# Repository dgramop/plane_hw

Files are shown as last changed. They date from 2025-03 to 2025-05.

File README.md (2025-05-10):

# Plane Hardware

Board Design Rev1 Mistakes:
- Wrong footprint for the PX4 connector on the pitot. Accidentally used the same one as all the I2C busses. Already have these connectors
- Forgot to order MALE connectors that go on the board. JST female is the for the cable. Whoops

Rev 2 Wishlist:
- Better harnessing - fewer things to connect + better modularity. Then we can have test beds for each part in isolation

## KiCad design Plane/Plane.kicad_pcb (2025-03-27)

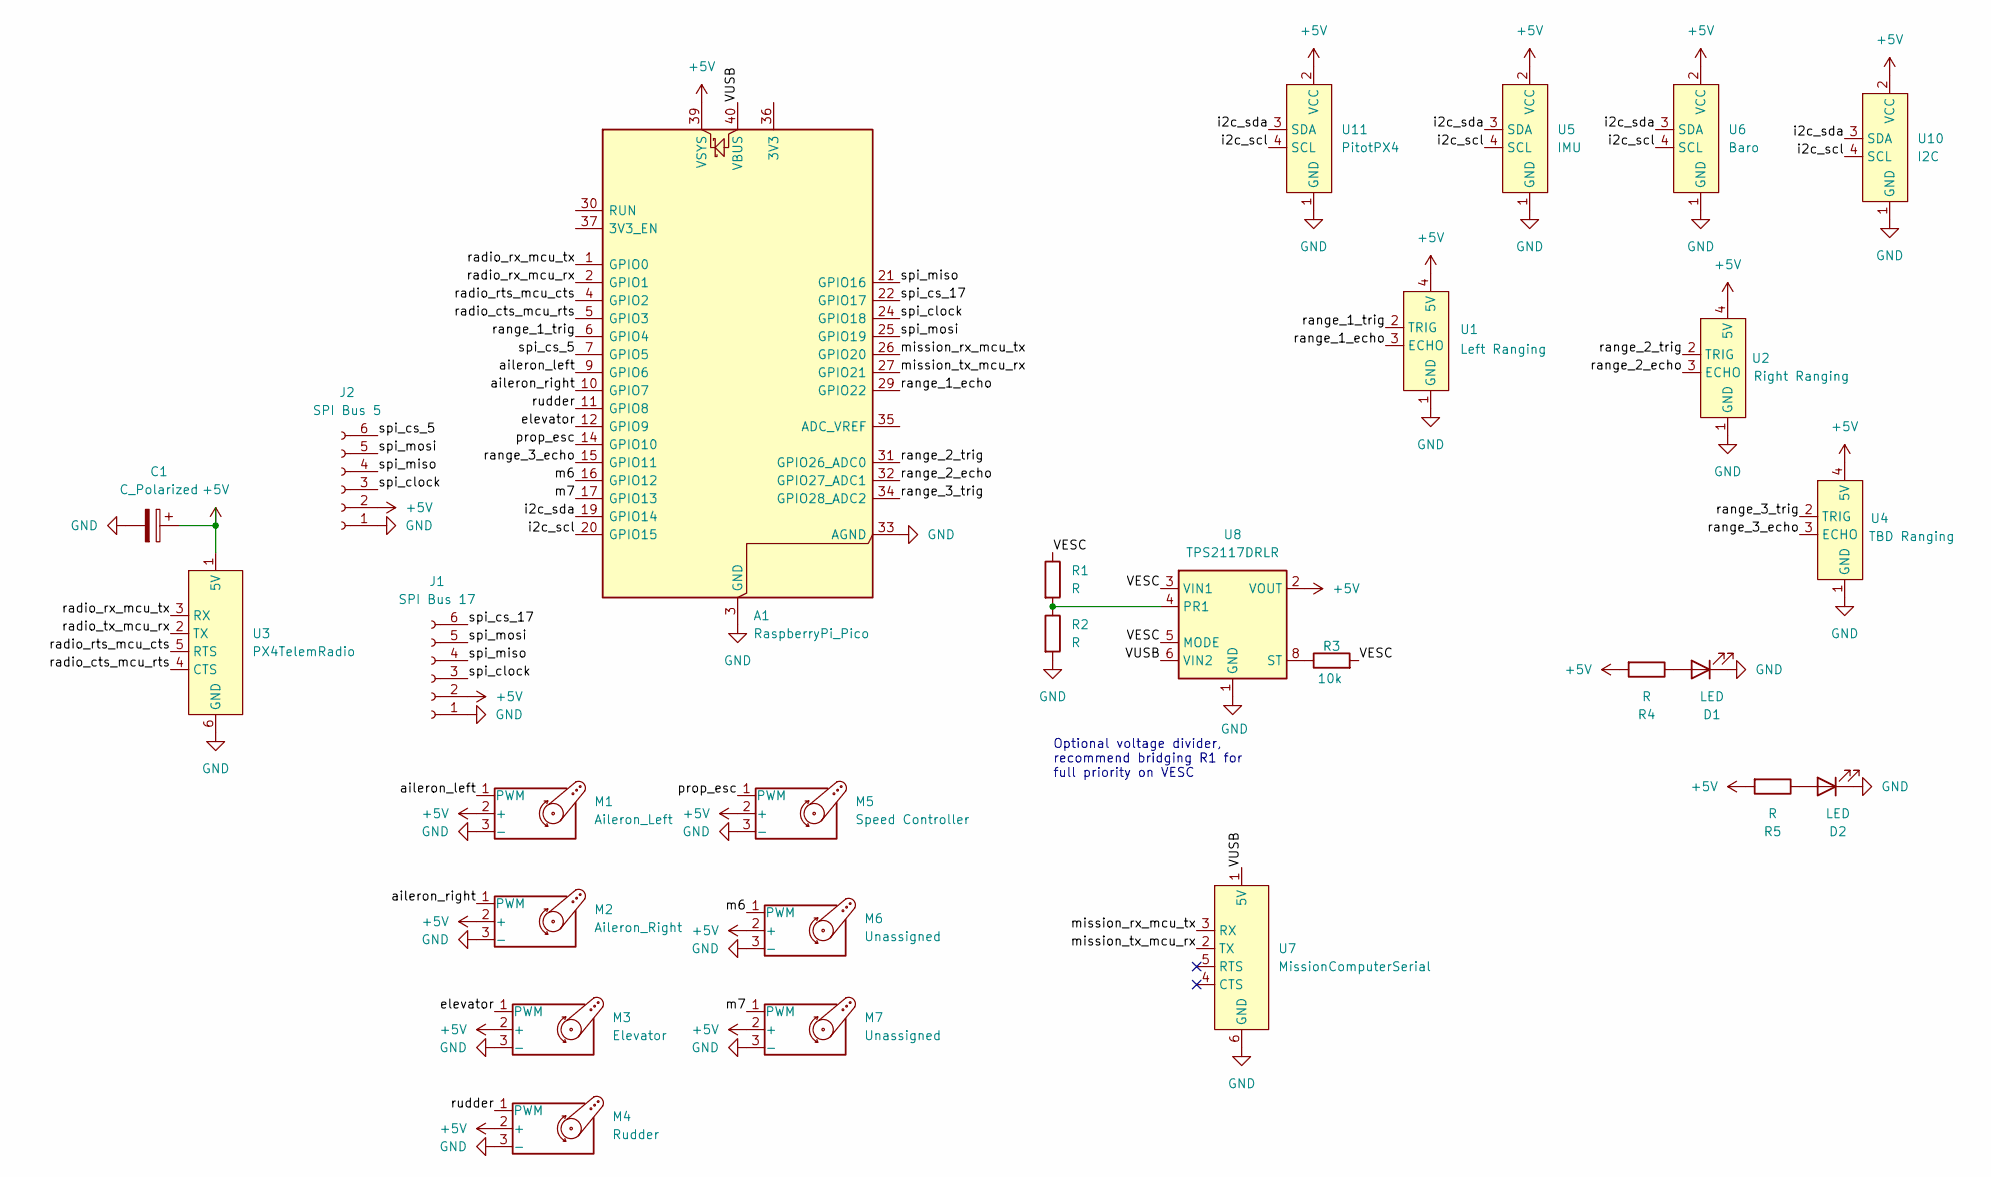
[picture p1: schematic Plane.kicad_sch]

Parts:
A1: RaspberryPi_Pico; RaspberryPi_Pico_Common_Unspecified
C1: C_Polarized; CP_Radial_D6.3mm_P2.50mm
D1, D2: LED; JST_PH_B2B-PH-K_1x02_P2.00mm_Vertical
J1: SPI Bus 17; JST_PH_B6B-PH-K_1x06_P2.00mm_Vertical
J2: SPI Bus 5; JST_PH_B6B-PH-K_1x06_P2.00mm_Vertical
M1: Aileron_Left; JST_PH_B3B-PH-K_1x03_P2.00mm_Vertical
M2: Aileron_Right; JST_PH_B3B-PH-K_1x03_P2.00mm_Vertical
M3: Elevator; JST_PH_B3B-PH-K_1x03_P2.00mm_Vertical
M4: Rudder; JST_PH_B3B-PH-K_1x03_P2.00mm_Vertical
M5: Speed Controller; JST_PH_B3B-PH-K_1x03_P2.00mm_Vertical
M6, M7: Unassigned; JST_PH_B3B-PH-K_1x03_P2.00mm_Vertical
R1, R2, R4, R5: R; R_0805_2012Metric_Pad1.20x1.40mm_HandSolder
R3: 10k; R_0805_2012Metric_Pad1.20x1.40mm_HandSolder
U1: Left Ranging; JST_PH_B4B-PH-K_1x04_P2.00mm_Vertical
U2: Right Ranging; JST_PH_B4B-PH-K_1x04_P2.00mm_Vertical
U3: PX4TelemRadio; JST_GH_SM06B-GHS-TB_1x06-1MP_P1.25mm_Horizontal
U4: TBD Ranging; JST_PH_B4B-PH-K_1x04_P2.00mm_Vertical
U5: IMU; JST_PH_B4B-PH-K_1x04_P2.00mm_Vertical
U6: Baro; JST_PH_B4B-PH-K_1x04_P2.00mm_Vertical
U7: MissionComputerSerial; JST_GH_SM06B-GHS-TB_1x06-1MP_P1.25mm_Horizontal
U8: TPS2117DRLR; SOT-583-8
U10: I2C; JST_PH_B4B-PH-K_1x04_P2.00mm_Vertical
U11: PitotPX4; JST_PH_B4B-PH-K_1x04_P2.00mm_Vertical

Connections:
+5V: A1.39 (VSYS), C1.1, J1.2, J2.2, M1.2 (+), M2.2 (+), M3.2 (+), M4.2 (+), M5.2 (+), M6.2 (+), M7.2 (+), R4.2, R5.2, U1.4 (5V), U2.4 (5V), U3.1 (5V), U4.4 (5V), U5.2 (VCC), U6.2 (VCC), U8.2 (VOUT), U8.7 (VOUT), U10.2 (VCC), U11.2 (VCC)
/VESC: R1.1, R3.2, U8.3 (VIN1), U8.5 (MODE)
/VUSB: A1.40 (VBUS), U7.1 (5V), U8.6 (VIN2)
/aileron_left: A1.9 (GPIO6), M1.1 (PWM)
/aileron_right: A1.10 (GPIO7), M2.1 (PWM)
/elevator: A1.12 (GPIO9), M3.1 (PWM)
/i2c_scl: A1.20 (GPIO15), U5.4 (SCL), U6.4 (SCL), U10.4 (SCL), U11.4 (SCL)
/i2c_sda: A1.19 (GPIO14), U5.3 (SDA), U6.3 (SDA), U10.3 (SDA), U11.3 (SDA)
/m6: A1.16 (GPIO12), M6.1 (PWM)
/m7: A1.17 (GPIO13), M7.1 (PWM)
/mission_rx_mcu_tx: A1.26 (GPIO20), U7.3 (RX)
/mission_tx_mcu_rx: A1.27 (GPIO21), U7.2 (TX)
/prop_esc: A1.14 (GPIO10), M5.1 (PWM)
/radio_cts_mcu_rts: A1.5 (GPIO3), U3.4 (CTS)
/radio_rts_mcu_cts: A1.4 (GPIO2), U3.5 (RTS)
/radio_rx_mcu_rx: A1.2 (GPIO1)
/radio_rx_mcu_tx: A1.1 (GPIO0), U3.3 (RX)
/radio_tx_mcu_rx: U3.2 (TX)
/range_1_echo: A1.29 (GPIO22), U1.3 (ECHO)
/range_1_trig: A1.6 (GPIO4), U1.2 (TRIG)
/range_2_echo: A1.32 (GPIO27_ADC1), U2.3 (ECHO)
/range_2_trig: A1.31 (GPIO26_ADC0), U2.2 (TRIG)
/range_3_echo: A1.15 (GPIO11), U4.3 (ECHO)
/range_3_trig: A1.34 (GPIO28_ADC2), U4.2 (TRIG)
/rudder: A1.11 (GPIO8), M4.1 (PWM)
/spi_clock: A1.24 (GPIO18), J1.3, J2.3
/spi_cs_5: A1.7 (GPIO5), J2.6
/spi_cs_17: A1.22 (GPIO17), J1.6
/spi_miso: A1.21 (GPIO16), J1.4, J2.4
/spi_mosi: A1.25 (GPIO19), J1.5, J2.5
GND: A1.3 (GND), A1.8 (GND), A1.13 (GND), A1.18 (GND), A1.23 (GND), A1.28 (GND), A1.33 (AGND), A1.38 (GND), C1.2, D1.1 (K), D2.1 (K), J1.1, J2.1, M1.3 (-), M2.3 (-), M3.3 (-), M4.3 (-), M5.3 (-), M6.3 (-), M7.3 (-), R2.2, U1.1 (GND), U2.1 (GND), U3.6 (GND), U4.1 (GND), U5.1 (GND), U6.1 (GND), U7.6 (GND), U8.1 (GND), U10.1 (GND), U11.1 (GND)
unnamed: D1.2 (A), R4.1
unnamed: D2.2 (A), R5.1
unnamed: R1.2, R2.1, U8.4 (PR1)
unnamed: R3.1, U8.8 (ST)

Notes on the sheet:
Optional voltage divider, recommend bridging R1 for full priority on VESC

Board: 2 copper layers, 28 parts (0 on the bottom side), 33 nets, no tracks yet.

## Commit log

2025-03-24 hw and elec
    [Plane.kicad_pcb, Plane.kicad_sch]
2025-03-26 fix some mistakes and connect power mux
    [Plane.kicad_sch]
2025-03-26 init board
    [Plane.kicad_pcb, Plane.kicad_sch]
2025-03-27 swap resistors to 0805, move stuff around
    [Plane.kicad_pcb, Plane.kicad_sch]
